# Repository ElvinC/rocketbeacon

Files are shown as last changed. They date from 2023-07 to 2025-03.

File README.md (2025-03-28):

# rocketbeacon
Configurable sub-GHz radio beacon for amateur rocketry.

**Warning: make sure to comply with your local RF regulations. Some frequency bands require an amateur radio license, others have power or duty cycle limitations.**

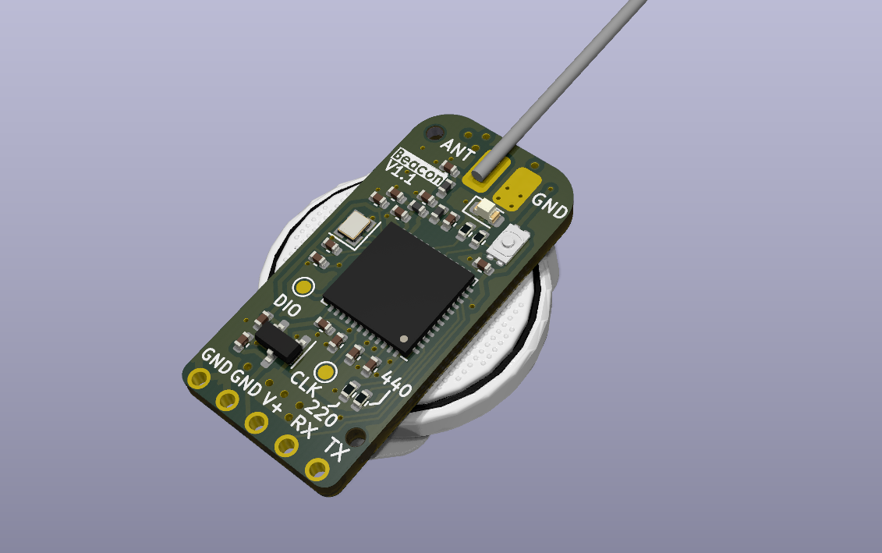
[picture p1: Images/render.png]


## Hardware V1.0
The hardware is designed in KiCad for assembly with JLCPCB. Two versions of the RF front end are available, one optimized for the 220 MHz band and one for the 440 MHz band.

The hardware features:

* STM32WLE5 wireless microcontroller
* Max 22 dBm output power
* CR2032 battery holder
* Can be powered externally by 3.3-5V

## Battery selection and life
**Warning: the beacon doesn't have reverse polarity protection, always double check the battery polarity!** If powered by an external battery (e.g. 1s lipo), connect to the V+ and GND pins. 

CR2032 batteries can't supply much current. When using CR2032 batteries, transmit powers above 16 dBm are not recommended without proper testing. When the voltage drops below 1.8V, the module restarts. An initial delay of a few seconds is thus recommended to allow CR2032 batteries to "recover" after a reset.

To give an idea of the battery life: 3x200 ms beeps at -9, 2, 14 dBm at 4 second intervals achieved 20 hours of battery life with the CR2032. 

Using LiPo batteries, transmit powers up to 22 dBm can be used without issues.

## Assembly V1.1
V1.1 is has some minor tweaks: Larger battery solder pads for improved durability, removal of an unnecessary rx component, and silkscreen tweaks.
The assembled PCB can be ordered by uploading the files from the 1.1 release to JLCPCB. `BOM-beacon-v1.1-440MHz.csv` or `BOM-beacon-v1.1-440MHz.csv` are the BOMs for each frequency version (pick one). Make sure visually that all components (except the 220/440 indicator resistor) are populated.

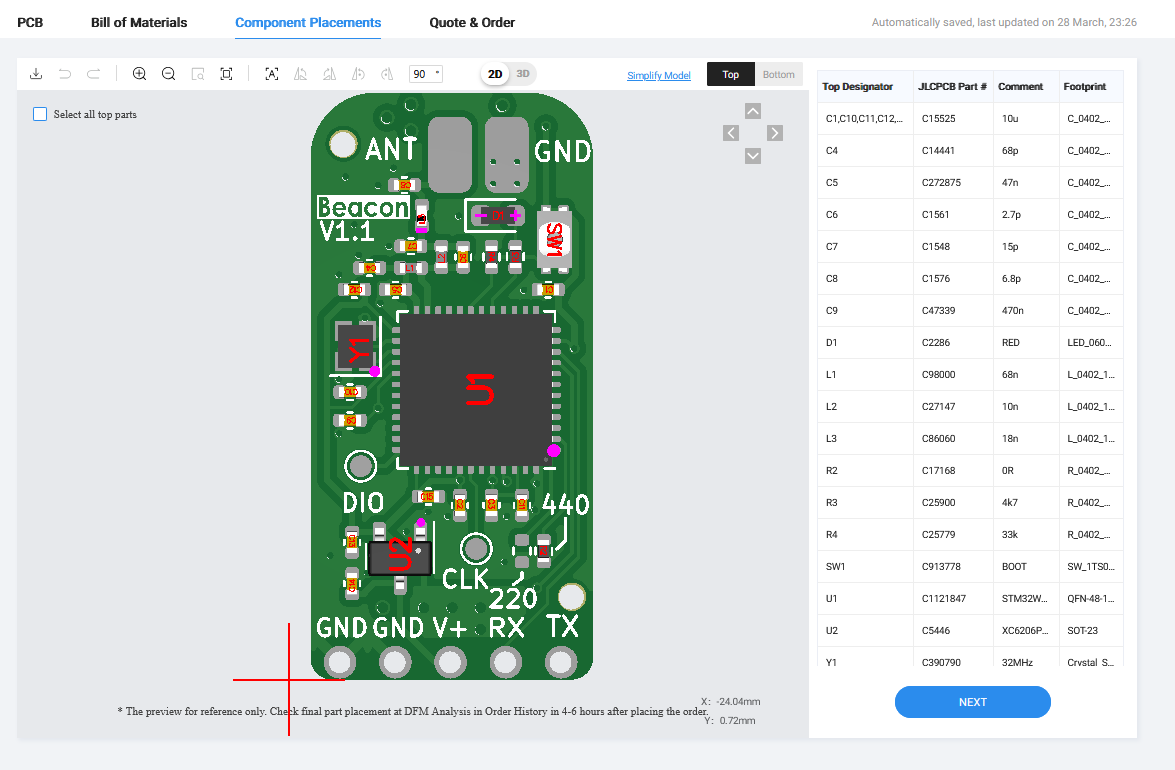
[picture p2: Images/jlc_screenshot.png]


Some BOM parts may be unavailable at the time of ordering, requiring alternative parts to be selected:

* STM32WLE5CBU6 alternatives: STM32WLE5CCU6 (other in the same family should work too without firmware changes)
* Crystal alternatives: Most 32MHz 10pF 10ppm crystals in the 2016 package should work. E.g. S2132000101080 (though default calibration might be off)
* Capacitor alternatives: Same values in the same package
* Inductors: Same values in the same package

Use the following settings when ordering:

* Layers=2
* Thickness=1.6
* Vias=Tented
* Remove order number=Specify a location
* PCBA type=Economic
* Assembly side=Top side
* Tooling holes = Added by Customer

## Assembly V1.0
The assembled PCB can be ordered by uploading the files from `Hardware\beacon\jlcpcb\production_files\V1.0` to JLCPCB. These files are also available in releases as a zip file. `GERBER-beacon.zip` contains the PCB files. For the pick-and-place centroid file, pick either `CPL-beacon-no-pinheader.csv` (cheaper and more compact) or `CPL-beacon-with-pinheader.csv` (assembled with pinheader). `BOM-beacon-v1.0-440MHz.csv` or `BOM-beacon-v1.0-440MHz.csv` are the BOMs for each frequency version (pick one). Make sure visually that all components (except the 220/440 indicator resistor) are populated. If the default STM32WLE5CBU6 is unavailable, the STM32WLE5CCU6 can be selected instead (works with the same firmware).

Use the following settings when ordering:

* Layers=2
* Thickness=1.6
* Vias=Tented
* Remove order number=Specify a location
* PCBA type=Economic
* Assembly side=Top side
* Tooling holes = Added by Customer

## Soldering

Other than the assembled PCB, an antenna is required. For a basic quarter wave copper antenna, you can use `length = 0.95 * 0.25 * speed of light / frequency`, where 0.95 is the velocity factor of copper. E.g.

* For 433 MHz, use a 165mm
* For 220 MHz band, Use 324mm

If powered by a button cell battery, solder on a [MY-2032-12](https://www.lcsc.com/product-detail/Battery-Connectors_MYOUNG-MY-2032-12_C964833.html) battery connector. Other similar CR2032 holders work as well, but may require trimming the solder leads to fit the footprint. Melt a little solder on the negative battery terminal before soldering on the battery holder to ensure proper electrical contact.

## Compile and program
The firmware can be modified and compiled with [STM32CubeIDE](https://www.st.com/en/development-tools/stm32cubeide.html).

The main code is located in `Firmware\Core\Src\main.c`. There are three main functions used to generate RF signals:

* `FSKBeep(int8_t powerdBm, uint32_t toneHz, uint32_t lengthMs)`: Synthesize a FSK sequence of alternating 1s and 0s. With a FM receiver, it sounds like a constant audio tone at `toneHz`.
* `CWBeep(int8_t powerdBm, uint32_t lengthMs)`: Generate a continuous wave tone. E.g. for morse code

Note that the `powerdBm` value can range from -9 to 22 dBm. `HAL_Delay(uint32_t millis)` can be used as delay.

Additionally, `play_morse_word(uint8_t* letters, uint8_t len, bool use_cw)` can be used to send an array of letters as morse (either FM or CW).

The default firmware allows for generation of regular FSK or CW tones at various power levels, with options for transmitting callsigns.

Programming the firmware can be done with [STM32CubeProg](https://www.st.com/en/development-tools/stm32cubeprog.html) and a cheap UART to USB dongle (If you don't have one, search "FTDI adaptor" and get one of the red dongles with 6 pins)

* Disconnect power
* Hold down the button
* Set UART adaptor to output 5V power with the jumper, though 3.3V should work as well.
* Connect the UART adaptor to the beacon (make sure Rx->Tx, Tx->Rx, GND->GND and VCC->V+). If unsoldered, hold them at an angle to ensure proper contact as shown below.
* LED should be continuously ON, indicating it has entered bootloader mode.
* In STM32CubeProg, select the UART option and port. Then connect to the MCU.
* In the Erasing & Programming tab, pick the right firmware `Firmware\Debug\rocketbeacon.elf`, and program
* Cycle power to execute the code.

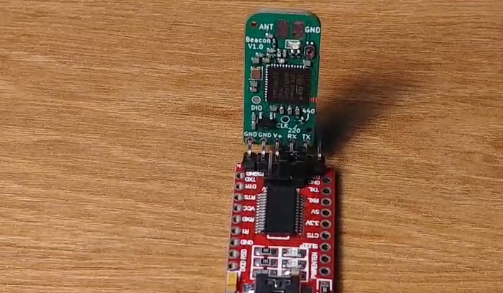
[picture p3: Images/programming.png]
programming


## Reception and tuning
Tune your radio to the programmed frequency. Without calibration, the frequency has a tolerance of roughly +/- 5 KHz in the 70 cm band.

## License and usage
Feel free to use or adapt the hardware design, though if you're a vendor interested in distributing these, please reach out to me at elvin (at) gyroflow.xyz :)

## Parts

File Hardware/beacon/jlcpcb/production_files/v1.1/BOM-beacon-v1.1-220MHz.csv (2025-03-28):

Comment | Designator | Footprint | LCSC
STM32WLE5CBUx | U1 | QFN-48-1EP_7x7mm_P0.5mm_EP5.6x5.6mm | C1121847
68p | C4 | C_0402_1005Metric | C14441
39p | C7 | C_0402_1005Metric | C106223
10u | C1,C10,C11,C12,C13,C14,C15,C2,C3 | C_0402_1005Metric | C15525
8.2p | C6 | C_0402_1005Metric | C325456
12p | C8 | C_0402_1005Metric | C1547
RED | D1 | LED_0603_1608Metric | C2286
33k | R4 | R_0402_1005Metric | C25779
4k7 | R3 | R_0402_1005Metric | C25900
15n | L2 | L_0402_1005Metric | C27143
47n | C5 | C_0402_1005Metric | C272875
32MHz | Y1 | Crystal_SMD_2016-4Pin_2.0x1.6mm | C383840
470n | C9 | C_0402_1005Metric | C47339
XC6206P332MR | U2 | SOT-23 | C5446
36n | L3 | L_0402_1005Metric | C2046147
BOOT | SW1 | SW_1TS026A | C913778
160n | L1 | L_0402_1005Metric | C413908
0R | R1 | R_0402_1005Metric | C17168
DNP | R2 | R_0402_1005Metric
Battery_Cell | BT1 | MY-2032-12

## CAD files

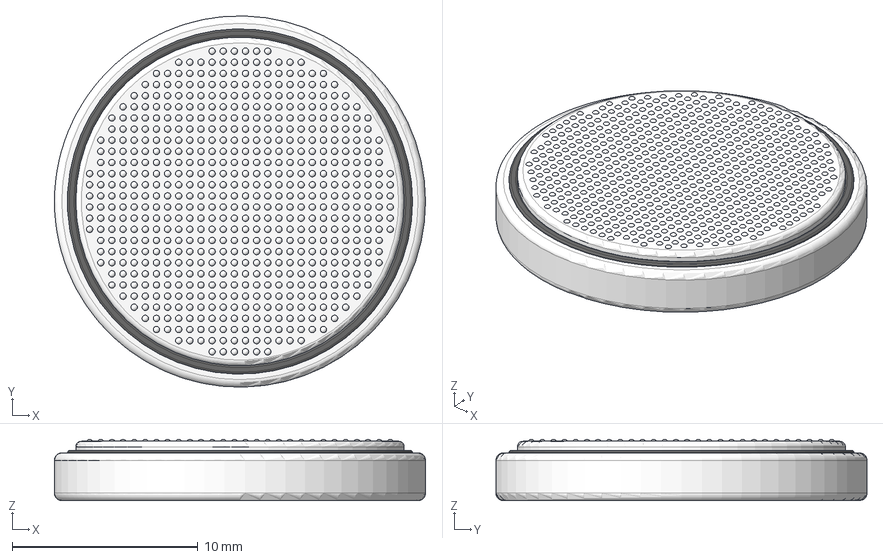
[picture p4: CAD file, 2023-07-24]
Hardware/beacon/3dmodels/cr2032_cell.step
20.0 x 20.0 x 3.30 mm

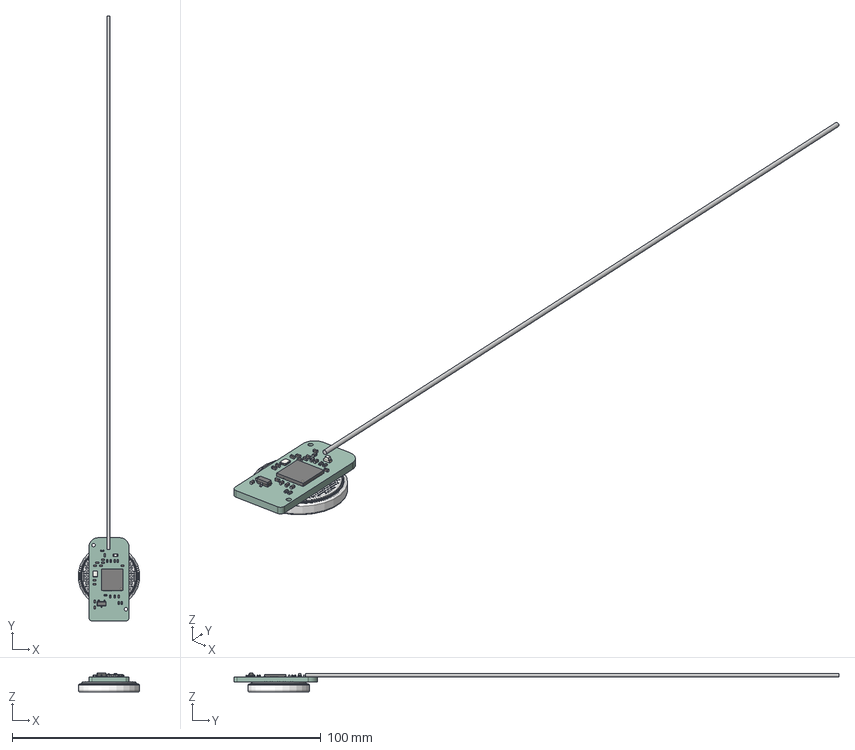
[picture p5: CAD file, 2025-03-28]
Hardware/beacon/beacon_v1.1.step
19.9 x 196.1 x 6.10 mm
L_0402_1005Metric x 3
C_0402_1005Metric x 15
QFN-48-1EP_7x7mm_Pitch0.5mm
R_0402_1005Metric x 4
SOT_23
Crystal_SMD_3225-4Pin_3.2x2.5mm
LED_0603_1608Metric
whipantenna v1
_autosave-beacon_PCB

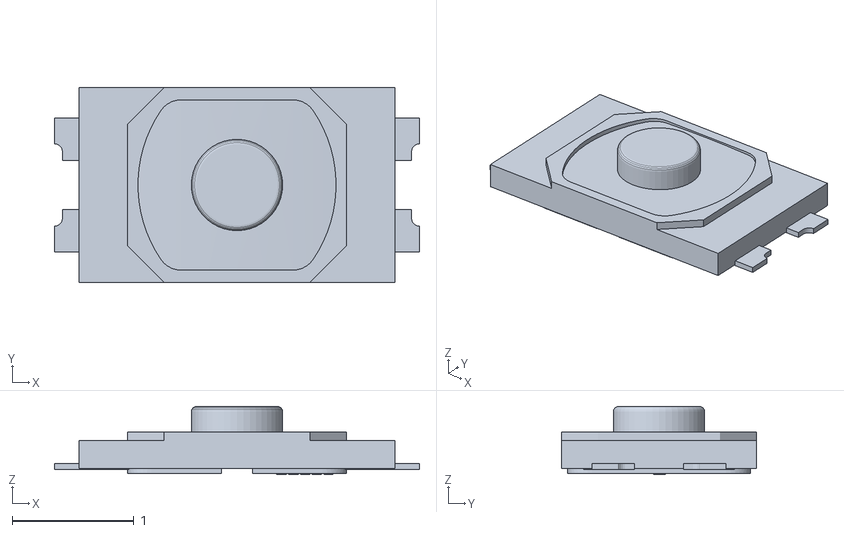
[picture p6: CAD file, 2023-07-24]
Hardware/beacon/3dmodels/1TS026A-1000-0550-CT.obj
3.00 x 1.60 x 0.56

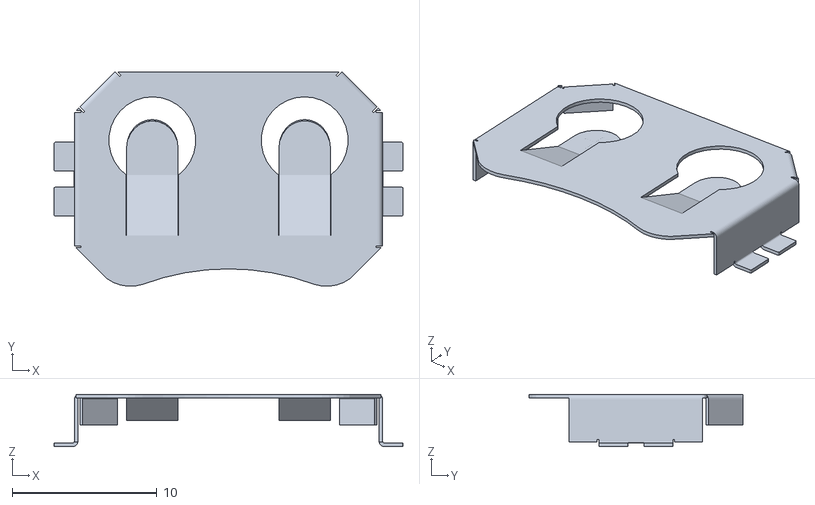
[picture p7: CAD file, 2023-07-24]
Hardware/beacon/3dmodels/cr2032.obj
24.1 x 14.8 x 3.60

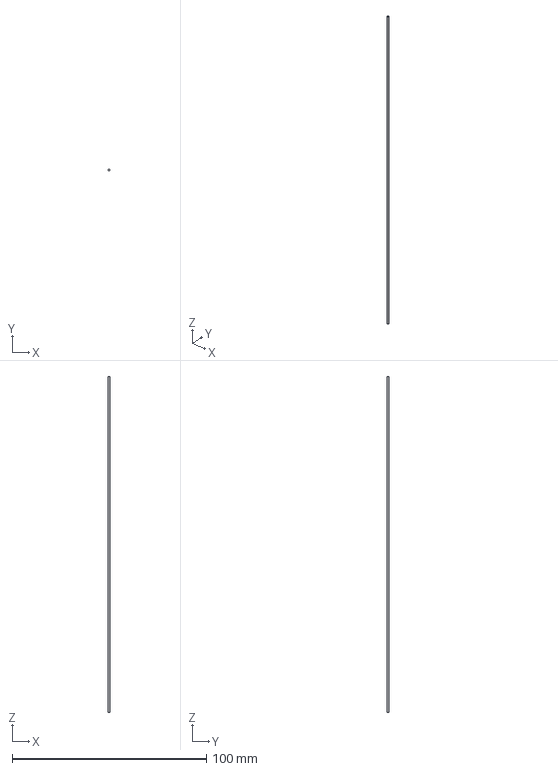
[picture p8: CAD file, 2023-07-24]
Hardware/beacon/3dmodels/whipantenna.step
0.999 x 1 x 173.0 mm

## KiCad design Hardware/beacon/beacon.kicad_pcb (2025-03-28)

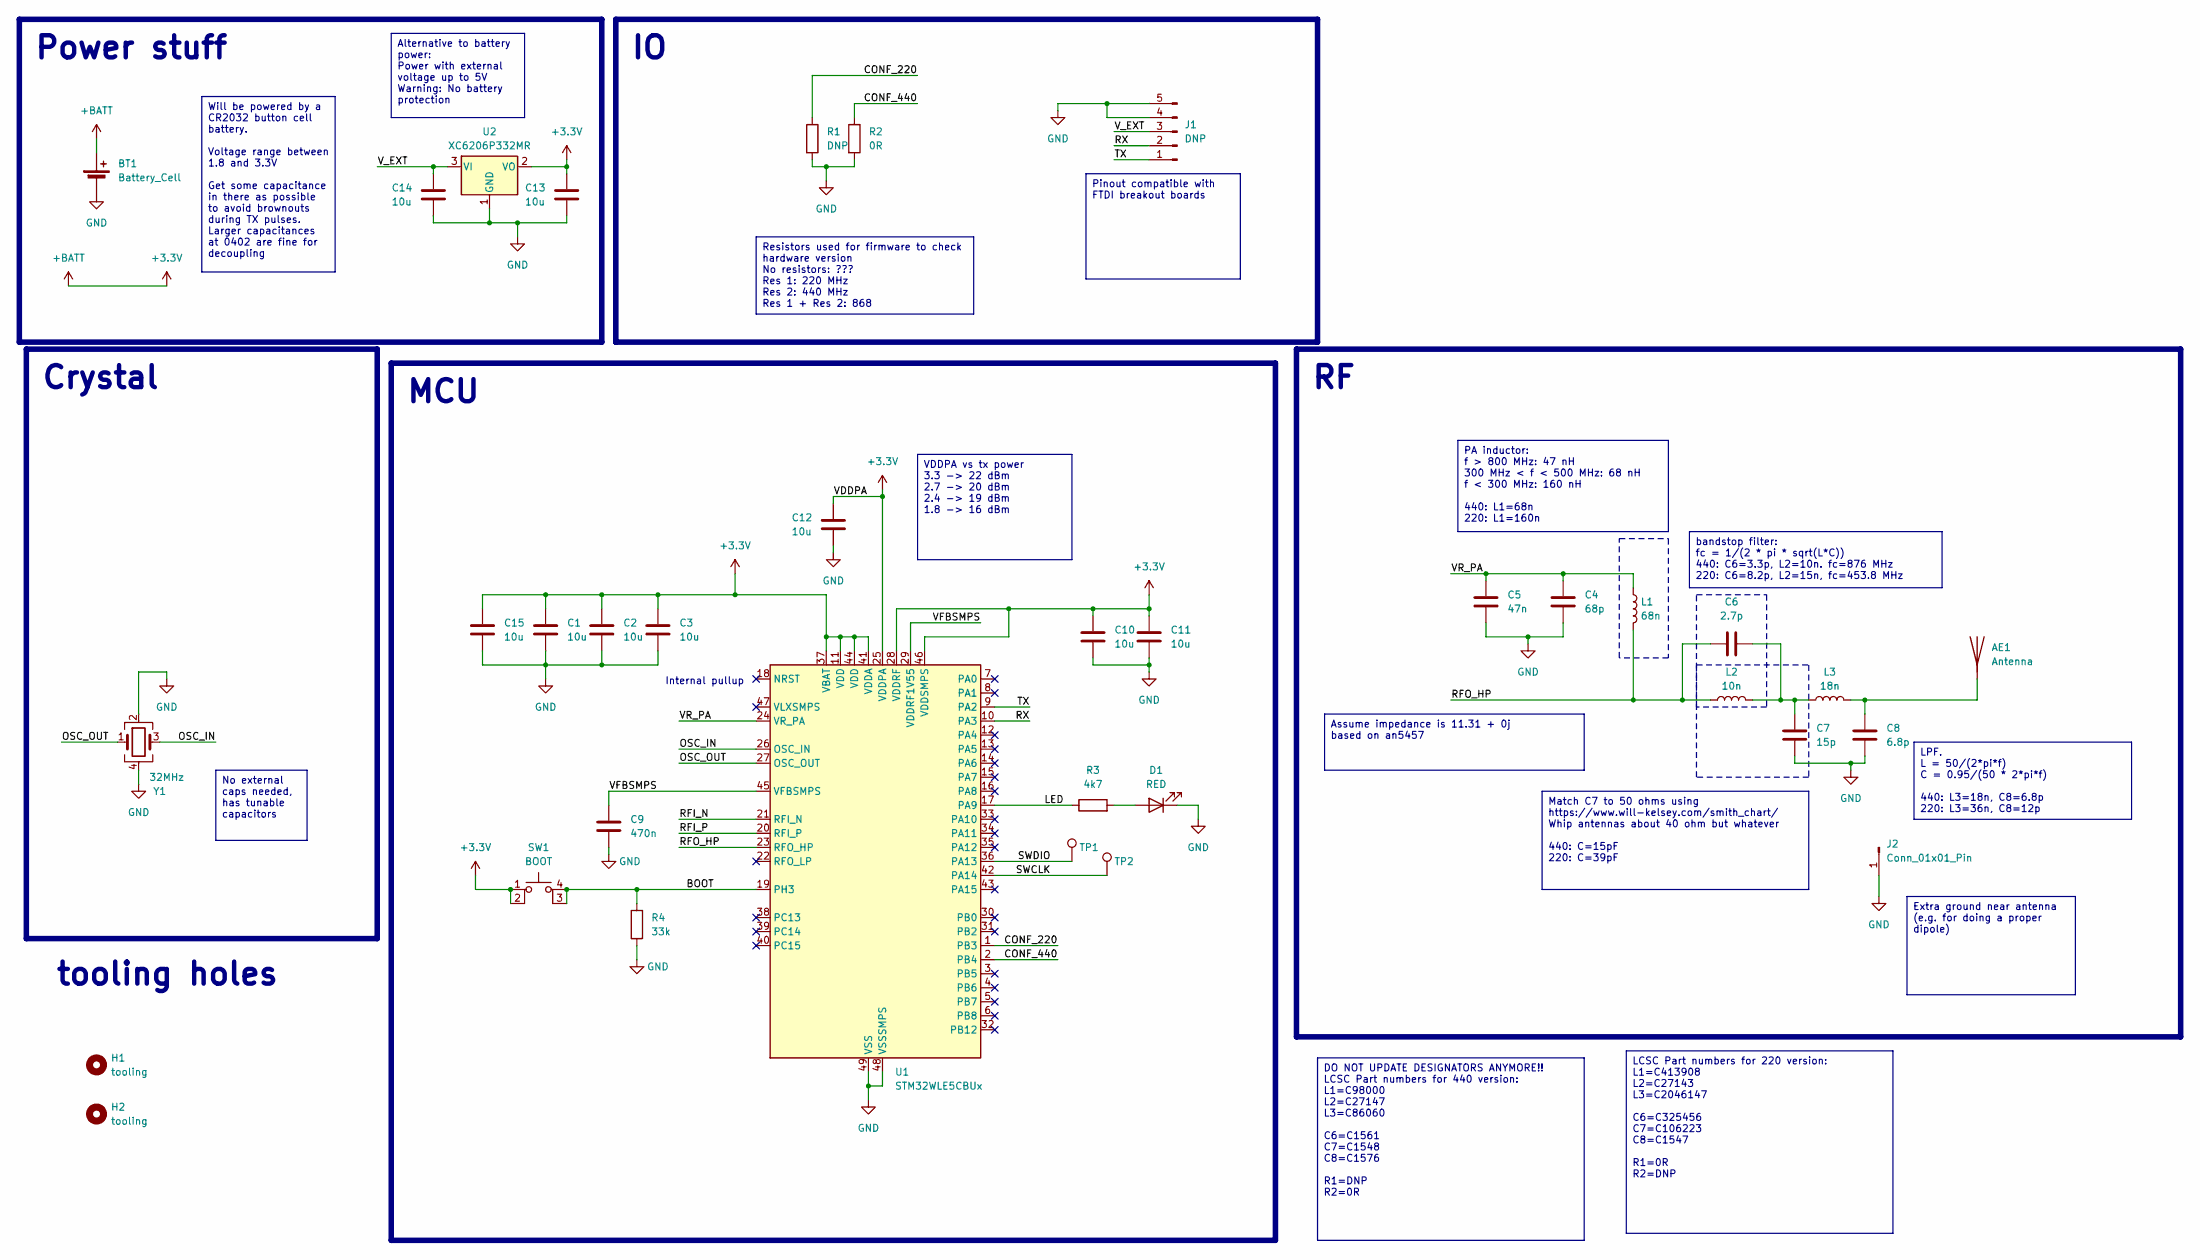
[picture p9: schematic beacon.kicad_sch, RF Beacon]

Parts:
AE1: Antenna; whip_antenna
BT1: Battery_Cell; MY-2032-12
C1, C2, C3, C10, C11, C12, C13, C14, C15: 10u; C_0402_1005Metric
C4: 68p; C_0402_1005Metric
C5: 47n; C_0402_1005Metric
C6: 2.7p; C_0402_1005Metric
C7: 15p; C_0402_1005Metric
C8: 6.8p; C_0402_1005Metric
C9: 470n; C_0402_1005Metric
D1: RED; LED_0603_1608Metric
H1, H2: tooling; toolinghole
J1: DNP; PinHeader_1x05_P2.54mm_Horizontal
J2: Conn_01x01_Pin; small_pad
L1: 68n; L_0402_1005Metric
L2: 10n; L_0402_1005Metric
L3: 18n; L_0402_1005Metric
R1: DNP; R_0402_1005Metric
R2: 0R; R_0402_1005Metric
R3: 4k7; R_0402_1005Metric
R4: 33k; R_0402_1005Metric
SW1: BOOT; SW_1TS026A
TP1, TP2: TestPoint_Pad_D1.0mm
U1: STM32WLE5CBUx; QFN-48-1EP_7x7mm_P0.5mm_EP5.6x5.6mm
U2: XC6206P332MR; SOT-23
Y1: 32MHz; Crystal_SMD_2016-4Pin_2.0x1.6mm; LCSC C383840

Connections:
+3.3V: BT1.1 (+), C1.1, C2.1, C3.1, C10.1, C11.1, C12.1, C13.1, C15.1, SW1.1, SW1.2, U1.11 (VDD), U1.25 (VDDPA), U1.28 (VDDRF), U1.37 (VBAT), U1.41 (VDDA), U1.44 (VDD), U1.46 (VDDSMPS), U2.2 (VO)
/BOOT: R4.2, SW1.3 (K), SW1.4 (A), U1.19 (PH3)
/CONF_220: R1.1, U1.1 (PB3)
/CONF_440: R2.1, U1.2 (PB4)
/LED: R3.1, U1.17 (PA9)
/OSC_IN: U1.26 (OSC_IN), Y1.3
/OSC_OUT: U1.27 (OSC_OUT), Y1.1
/RFI_N: U1.21 (RFI_N)
/RFI_P: U1.20 (RFI_P)
/RFO_HP: C6.1, L1.2, L2.1, U1.23 (RFO_HP)
/RX: J1.2, U1.10 (PA3)
/SWCLK: TP2.1, U1.42 (PA14)
/SWDIO: TP1.1, U1.36 (PA13)
/TX: J1.1, U1.9 (PA2)
/VFBSMPS: C9.1, U1.29 (VDDRF1V55), U1.45 (VFBSMPS)
/VR_PA: C4.1, C5.1, L1.1, U1.24 (VR_PA)
/V_EXT: C14.1, J1.3, U2.3 (VI)
GND: BT1.2 (-), C1.2, C2.2, C3.2, C4.2, C5.2, C7.2, C8.2, C9.2, C10.2, C11.2, C12.2, C13.2, C14.2, C15.2, D1.1 (K), J1.4, J1.5, J2.1, R1.2, R2.2, R4.1, U1.48 (VSSSMPS), U1.49 (VSS), U2.1 (GND), Y1.2, Y1.4
unnamed: AE1.1 (A), C8.1, L3.2
unnamed: C6.2, C7.1, L2.2, L3.1
unnamed: D1.2 (A), R3.2

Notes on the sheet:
No external caps needed, has tunable capacitors
Match C7 to 50 ohms using https://www.will-kelsey.com/smith_chart/ Whip antennas about 40 ohm but whatever 440: C=15pF 220: C=39pF
Resistors used for firmware to check hardware version No resistors: ??? Res 1: 220 MHz Res 2: 440 MHz Res 1 + Res 2: 868
PA inductor: f > 800 MHz: 47 nH 300 MHz < f < 500 MHz: 68 nH f < 300 MHz: 160 nH 440: L1=68n 220: L1=160n
Extra ground near antenna (e.g. for doing a proper dipole)
bandstop filter: fc = 1/(2 * pi * sqrt(L*C)) 440: C6=3.3p, L2=10n. fc=876 MHz 220: C6=8.2p, L2=15n, fc=453.8 MHz
VDDPA vs tx power 3.3 -> 22 dBm 2.7 -> 20 dBm 2.4 -> 19 dBm 1.8 -> 16 dBm
LCSC Part numbers for 220 version: L1=C413908 L2=C27143 L3=C2046147 C6=C325456 C7=C106223 C8=C1547 R1=0R R2=DNP
Will be powered by a CR2032 button cell battery. Voltage range between 1.8 and 3.3V Get some capacitance in there as possible to avoid brownouts during TX pulses. Larger capacitances at 0402 are fine for decoupling
Assume impedance is 11.31 + 0j based on an5457
LPF. L = 50/(2*pi*f) C = 0.95/(50 * 2*pi*f) 440: L3=18n, C8=6.8p 220: L3=36n, C8=12p
Pinout compatible with FTDI breakout boards
Alternative to battery power: Power with external voltage up to 5V Warning: No battery protection
DO NOT UPDATE DESIGNATORS ANYMORE!! LCSC Part numbers for 440 version: L1=C98000 L2=C27147 L3=C86060 C6=C1561 C7=C1548 C8=C1576 R1=DNP R2=0R
tooling holes
Power stuff
MCU
Crystal
Internal pullup

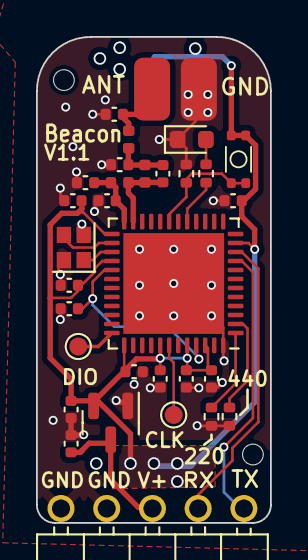
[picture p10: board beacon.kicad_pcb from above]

Board: 2 copper layers, 13.0 x 27.0 mm, 35 parts (1 on the bottom side), 19 nets.

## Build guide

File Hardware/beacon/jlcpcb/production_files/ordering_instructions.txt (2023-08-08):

JLCPCB Ordering options. If not specified, use defaults.

Layers=2
Thickness=1.6
Vias=Tented
Remove order number=Specify a location
PCBA type=Economic
Assembly side=Top side
Tooling holes = Added by Customer

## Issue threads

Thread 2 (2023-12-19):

Issue with ordering from JLCPCB

AD2GF, 2023-12-19:
I attempted to order the 440MHz beacon from JLCPCB, but due to the component 'R2' I am unable to select Economic PCB Assembly, apparently due to the small footprint size of the component. Changing to Standard PCB Assembly ends up adding $50 to the order. The component has a resistance of zero ohms, and it says in the schematic that its only used for telling the firmware whether the beacon is 220MHz/440MHz. Therefore, I plan on removing the resistor from the order, and just bridging the 440MHz pads with solder. I just wanted to confirm whether or not it is safe to do this.

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
ㅤ
ㅤ

ㅤ

In addition, there are 5 components that JLCPCB is unable to find a part for. I assume that the whip antenna, tooling holes, and DNP resistor are not meant to actually populate the PCB, but I wasn't sure if the small connection pad was also supposed to show up as missing.
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

ElvinC, 2023-12-19:
Looks like it selected the wrong package for some reason for the resistor (currently just a visual indicator and not actually implemented in the firmware). You can use C17168 for the 0402 0R resistor. I'll fix the bom files with the proper part numbers at some point

ElvinC, 2023-12-19:
Out of curiosity, how did you find out about this project?

justinkoshy, 2023-12-19:
I was looking for a cheap RDF tracker, there was a thread in the r/rocketry subreddit linking this github. Thanks for the help!

ElvinC, 2023-12-20:
Just keeping this open as a reminder to fix the BOM stuff

Closed 2025-03-28.

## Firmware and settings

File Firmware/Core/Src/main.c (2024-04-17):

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
/* Includes ------------------------------------------------------------------*/
#include "main.h"

/* USER CODE BEGIN Includes */
#include <stdbool.h>
#include <string.h>
#include <math.h>
/* USER CODE END Includes */

ADC_HandleTypeDef hadc;

CRC_HandleTypeDef hcrc;

SUBGHZ_HandleTypeDef hsubghz;

UART_HandleTypeDef huart2;

void SystemClock_Config(void);
static void MX_GPIO_Init(void);
static void MX_ADC_Init(void);
static void MX_SUBGHZ_Init(void);
static void MX_USART2_UART_Init(void);
static void MX_CRC_Init(void);
/* USER CODE BEGIN PFP */

void SetStandbyXOSC();
void SetPacketTypeLora();
void SetPacketTypeFSK();
uint32_t ComputeRfFreq(double frequencyMhz);
void SetRfFreq(uint32_t rfFreq);
void SetPaLowPower();
void SetPa22dB();
void SetTxPower(int8_t powerdBm);
void SetContinuousWave();
void SetTxInfinitePreamble();
void SetTx(uint32_t timeout);
void SetRx(uint32_t timeout);
void SetModulationParamsLora(const uint8_t params[4]);
void SetModulationParamsFSK(uint32_t bitrate, uint8_t pulseshape, uint8_t bandwidth, uint32_t freq_dev);
void SetPacketParamsLora(uint16_t preamble_length, bool header_fixed, uint8_t payload_length, bool crc_enabled, bool invert_iq);
void FSKBeep(int8_t powerdBm, uint32_t toneHz, uint32_t lengthMs);
void CWBeep(int8_t powerdBm, uint32_t lengthMs);

/* USER CODE END PFP */

/* USER CODE BEGIN 0 */

// standard frequencies. Note: zero indexed.
const double LPD433[69] = {
    433.075, 433.100, 433.125, 433.150, 433.175, 433.200, 433.225, 433.250, 433.275, 433.300, // 1-10
    433.325, 433.350, 433.375, 433.400, 433.425, 433.450, 433.475, 433.500, 433.525, 433.550, // 11-20
    433.575, 433.600, 433.625, 433.650, 433.675, 433.700, 433.725, 433.750, 433.775, 433.800, // 21-30
    433.825, 433.850, 433.875, 433.900, 433.925, 433.950, 433.975, 434.000, 434.025, 434.050, // 31-40
    434.075, 434.100, 434.125, 434.150, 434.175, 434.200, 434.225, 434.250, 434.275, 434.300, // 41-50
    434.325, 434.350, 434.375, 434.400, 434.425, 434.450, 434.475, 434.500, 434.525, 434.550, // 51-60
    434.575, 434.600, 434.625, 434.650, 434.675, 434.700, 434.725, 434.750, 434.775           // 61-69
};

const double PMR446[16] = {
    446.00625, 446.01875, 446.03125, 446.04375, 446.05625, // 1-5
    446.06875, 446.08125, 446.09375, 446.10625, 446.11875, // 6-10
    446.13125, 446.14375, 446.15625, 446.16875, 446.18125, // 11-15
    446.19375 // 16
};

const double FRS[22] = {
    462.5625, 462.5875, 462.6125, 462.6375, 462.6625, 462.6875, 462.7125, 467.5625, 467.5875, 467.6125, // 1-10
    467.6375, 467.6625, 467.6875, 467.7125, 462.5500, 462.5750, 462.6000, 462.6250, 462.6500, 462.6750, // 11-20
    462.7000, 462.7250 // 21-22
};


// letter to morse based on ASCII characters.
// right-terminated by a "1". 1 is dah, 0 is dit.
const uint8_t morse_chars[] = {
    0b11111111,       // Special code for SPACE
    0b10000000,       // N/A
    0b10000000,       // N/A
    0b10000000,       // N/A
    0b10000000,       // N/A
    0b10000000,       // N/A
    0b10000000,       // N/A
    0b10000000,       // N/A
    0b10000000,       // N/A
    0b10000000,       // N/A
    0b10000000,       // N/A
    0b10000000,       // N/A
    0b10000000,       // N/A
    0b10000110,       // - Hyphen sign
    0b10000000,       // N/A
    0b10010100,       // "/" Slash
    0b11111100,       // "0"
    0b01111100,       // "1"
    0b00111100,       // "2"
    0b00011100,       // "3"
    0b00001100,       // "4"
    0b00000100,       // "5"
    0b10000100,       // "6"
    0b11000100,       // "7"
    0b11100100,       // "8"
    0b11110100,       // "9"
    0b10000000,       // N/A
    0b10000000,       // N/A
    0b10000000,       // N/A
    0b10001100,       // "=" BT prosign/Equal sign
    0b10000000,       // N/A
    0b00110010,       // "?" Question mark
    0b10000000,       // N/A
    0b01100000,       // "A"
    0b10001000,       // "B"
    0b10101000,       // "C"
    0b10010000,       // "D"
    0b01000000,       // "E"
    0b00101000,       // "F"
    0b11010000,       // "G"
    0b00001000,       // "H"
    0b00100000,       // "I"
    0b01111000,       // "J"
    0b10110000,       // "K"
    0b01001000,       // "L"
    0b11100000,       // "M"
    0b10100000,       // "N"
    0b11110000,       // "O"
    0b01101000,       // "P"
    0b11011000,       // "Q"
    0b01010000,       // "R"
    0b00010000,       // "S"
    0b11000000,       // "T"
    0b00110000,       // "U"
    0b00011000,       // "V"
    0b01110000,       // "W"
    0b10011000,       // "X"
    0b10111000,       // "Y"
    0b11001000,       // "Z"
    0b10000000,       // N/A
    0b10000000,       // N/A
    0b10000000,       // N/A
    0b10000000,       // N/A
    0b10000000,       // N/A
    0b10000000,       // N/A
    0b01100000,       // "a"
    0b10001000,       // "b"
    0b10101000,       // "c"
    0b10010000,       // "d"
    0b01000000,       // "e"
    0b00101000,       // "f"
    0b11010000,       // "g"
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
};

void LED_on() {
    HAL_GPIO_WritePin(LED_GPIO_Port, LED_Pin, GPIO_PIN_SET);
}
void LED_off() {
    HAL_GPIO_WritePin(LED_GPIO_Port, LED_Pin, GPIO_PIN_RESET);
}

// https://en.wikipedia.org/wiki/Morse_code#/media/File:International_Morse_Code.svg
uint32_t morse_unit_ms = 70;
int8_t morse_power = 10;

void play_morse_char(uint8_t ascii_letter, bool use_cw) {
    uint8_t morse_code = 0b11111111;
    if (ascii_letter > 31 && ascii_letter < 123) {
        morse_code = morse_chars[ascii_letter - 32];
    }

    // space
    if (morse_code == 0b11111111) {
        if (use_cw) {
            HAL_Delay(morse_unit_ms);
        } else {
            //FSKBeep(morse_power, 750, morse_unit_ms);
            HAL_Delay(morse_unit_ms);
        }
        return;
    }
    uint8_t terminatelen = 0;
    for (uint8_t idx = 0; idx < 8; idx++) {
        if (morse_code & (1 << idx)) {
            terminatelen = idx;
            break;
        }
    }

    for (uint8_t i = 7; i > terminatelen; i--) {
    	LED_on();
        if (morse_code & (1 << i)) {
            // make dat
            //printf("-");
            if (use_cw) {
                CWBeep(morse_power, morse_unit_ms * 3);
            } else {
                FSKBeep(morse_power, 400, morse_unit_ms * 3);
            }
        } else {
            // make dit
            //printf(".");
            if (use_cw) {
                CWBeep(morse_power, morse_unit_ms);
            } else {
                FSKBeep(morse_power, 400, morse_unit_ms);
            }
        }
        LED_off();

        // Make delay.
        if (use_cw) {
            HAL_Delay(morse_unit_ms);
        } else {
            HAL_Delay(morse_unit_ms);
            //CWBeep(morse_power, morse_unit_ms);
        }
    }
}

void play_morse_word(uint8_t* letters, uint8_t len, bool use_cw) {
    for (uint8_t i = 0; i < len; i++) {
        play_morse_char(letters[i], use_cw);

        // Space between letters
        if (use_cw) {
            HAL_Delay(morse_unit_ms * 3);
        } else {
            //CWBeep(morse_power, morse_unit_ms);
            HAL_Delay(morse_unit_ms * 3);
        }
    }
}


void rx_test(bool is_tx) {
  LED_on();
  HAL_Delay(100);
  LED_off();
  SetStandbyXOSC();
  HAL_Delay(1);
  SetPacketTypeLora();
  HAL_Delay(1);
  SetRfFreq(ComputeRfFreq(433.250));

  //SetPaLowPower(); // For powers up to 14 dBm
  SetPa22dB(); // Allows powers up to 22 dBm
  HAL_Delay(1);
  SetTxPower(-9);
  HAL_Delay(1);
  uint8_t LORA_SF12_BW62_CR45[4] = {0x0C, 0x03, 0x01, 0x00};
  SetModulationParamsLora(LORA_SF12_BW62_CR45);
  HAL_Delay(1);

  SetPacketParamsLora(4, true, 4, true, false); // Send 4 bytes
  HAL_Delay(1);
  uint8_t buffer[4] = {0x00, 0x00, 0x00, 0x00};
  HAL_SUBGHZ_WriteBuffer(&hsubghz, 0, buffer, 4);


  while (1) {
      if (is_tx) {
          buffer[0] = 0x04; // Led ON
          HAL_SUBGHZ_WriteBuffer(&hsubghz, 0, buffer, 4);
          HAL_Delay(1);
          SetTx(0);
          LED_on();
          HAL_Delay(1000);

      } else {
          SetRx(0);
          HAL_Delay(100);
          HAL_SUBGHZ_ReadBuffer(&hsubghz, 0, buffer, 4);
          if (buffer[0] == 0x04) {
              LED_on();

          } else {
              LED_off();
          }
      }
  }

}

/* USER CODE END 0 */

/**
  * @brief  The application entry point.
  * @retval int
  */
int main(void)
{
  /* MCU Configuration--------------------------------------------------------*/

  /* Reset of all peripherals, Initializes the Flash interface and the Systick. */
  HAL_Init();

  /* Configure the system clock */
  SystemClock_Config();

  /* Initialize all configured peripherals */
  MX_GPIO_Init();
  MX_ADC_Init();
  MX_SUBGHZ_Init();
  MX_USART2_UART_Init();
  MX_CRC_Init();
  /* USER CODE BEGIN 2 */

  // ==========================================
  //      START CHANGING SETTINGS HERE
  // ==========================================

  // Frequency setting in MHz
  // Can be a "standard" frequency, e.g. center_freq = LPD433[20-1]; sets it to LPD433 channel 20 (zero indexed) = 433.550 MHz
  double center_freq = 433.225;

  // max power in dBm, valid values between -9 and 22;
  // If using coin cell batteries, values above 16 dBm are not recommended without testing due to current limitations.
  // Alternatively use external LiPo power
  int maxPower = 10;

  double freq_correction = 0.99999539941; // For tuning frequency

  bool CallsignTF = false;
  uint8_t callsign[] = "nocall";

  int CallsignPeriod = 300; // seconds

  // Continuous Wave (CW) settings
  bool CWbeep = false;
  int CWbeepcount = 4;
  bool CWHigh2Low = true; //if true, start with highest power beep, decrease from there
  int CWbeepOffset = 150; //Hertz
  int CWbeepIndLength = 20; //milliseconds
  int CWbeepGapLength = 20; //milliseconds


  // Frequency-shift keying (FSK) settings. Can be heard with FM receivers
  bool FSKbeep = true;
  int FSKbeepcount = 3;
  bool FSKHigh2Low = false; //if true, start with highest power beep, decrease from there. When true, it maximizes the power of the highest power beep, but makes it harder to read a visible signal indicator on later beeps.
  int FSKbeepIndLength = 250; //milliseconds
  int FSKbeepGapLength = 50; //milliseconds
  bool CustomFSKtones = false;
  int CustomFSKfrequencies[] = {320, 400, 480, 640}; // Must match the length exactly!

  int Period = 2000; //milliseconds
  int StartupWait = 5000; // initial start. A few seconds to allow coin cell batteries to recover in case of brownout resets.

  // ==========================================
  //      STOP CHANGING SETTINGS HERE
  // ==========================================


  //EE_Status ee_status = EE_OK;
  LED_on();
  HAL_Delay(StartupWait);
  LED_off();
  SetStandbyXOSC();
  HAL_Delay(1);
  SetPacketTypeLora();
  HAL_Delay(1);

  //SetPaLowPower(); // For powers up to 14 dBm
  SetPa22dB(); // Allows powers up to 22 dBm
  HAL_Delay(1);
  SetTxPower(-9);
  HAL_Delay(1);

  SetPacketTypeFSK();

  SetModulationParamsFSK(2000,    0x09,     0x1E,      2500);


  //  int FSKtones[12] = {400, 350, 300, 250, 200, 150, 1600, 2000, 2400, 3200, 4000, 4800};
  int FSKtones[FSKbeepcount];
  SetRfFreq(ComputeRfFreq(center_freq * freq_correction));

  memset(FSKtones, 0, sizeof(FSKtones));
  for(int i=0; i<FSKbeepcount; i++){
      int base = floor(i/3);
      int mplr = 1<<base;
      FSKtones[i] = 320*(1 + 0.25*(i-3*floor(i/3)))*mplr;
  }
  if (CustomFSKtones){
      memcpy(FSKtones, CustomFSKfrequencies, sizeof(FSKtones));
  }

  /* USER CODE END 2 */

  /* Infinite loop */
  /* USER CODE BEGIN WHILE */

  /*
  while (1) {
      // Emulate comspec beacon at 40 mW
      LED_on();
      CWBeep(16, 50);
      LED_off();
      HAL_Delay(1000);
  }*/

  int loopCounter = floor(CallsignPeriod * 1000 / Period);

  int gap = Period;
  if(FSKbeep) {
	  gap = gap-(FSKbeepIndLength * FSKbeepcount);
	  gap = gap-(FSKbeepGapLength * (FSKbeepcount-1));
  }
  if(CWbeep) {
	  gap = gap-(CWbeepIndLength * CWbeepcount);
	  gap = gap-(CWbeepGapLength * (CWbeepcount - 1));
  }
  if (CWbeep && FSKbeep) {
	  gap = gap /2;
  }

  int FSKTXpwrs[FSKbeepcount];
  memset(FSKTXpwrs, 0, sizeof(FSKTXpwrs));
  if(FSKbeep){
	  int stepsize = 0;
	  if (FSKbeepcount > 1){
		  stepsize = (31 - 22 + maxPower)/(FSKbeepcount - 1);
	  }
	  for(int i=0; i<FSKbeepcount; i++){
		 FSKTXpwrs[i] = maxPower - stepsize * i;
	  }
  }
  int CWTXpwrs[CWbeepcount];
  memset(CWTXpwrs, 0, sizeof(CWTXpwrs));
  if(CWbeep){
	  int stepsize = 0;
	  if (CWbeepcount > 1){
		  stepsize = (31 - 22 + maxPower)/(CWbeepcount - 1);
	  }
	  for(int i=0; i<CWbeepcount; i++){
		 CWTXpwrs[i] = maxPower - stepsize * i;
	  }
  }

  while (1)
  {
	  if(CallsignTF)
	  {
		  play_morse_word(callsign, sizeof(callsign)-1, false);
	  }

      LED_off();

      HAL_Delay(gap);
      for (int i=0; i<loopCounter-1; i++)
      {
    	  SetRfFreq(ComputeRfFreq(center_freq * freq_correction));
    	  // FSK beeps
    	  if(FSKbeep){
    		  if(FSKHigh2Low){
    			  for (int j=0; j<FSKbeepcount; j++){
    				  LED_on();
    				  FSKBeep(FSKTXpwrs[j], FSKtones[j], FSKbeepIndLength);
    				  LED_off();
    				  HAL_Delay(FSKbeepGapLength);
    			  }
    		  }
    		  else {
    			  for (int j=0; j<FSKbeepcount; j++){
    				  LED_on();
    				  FSKBeep(FSKTXpwrs[FSKbeepcount-1-j], FSKtones[j], FSKbeepIndLength);
    				  LED_off();
    				  HAL_Delay(FSKbeepGapLength);
    			  }
    		  }
    		  HAL_Delay(gap);
    	  }
    	  if(CWbeep){
    		  if(CWHigh2Low){
    			  for (int j=0; j<CWbeepcount; j++){
    				  LED_on();
    				  SetRfFreq(ComputeRfFreq((center_freq + 0.000001*CWbeepOffset*j) * freq_correction));
    				  CWBeep(CWTXpwrs[j], CWbeepIndLength);
    				  LED_off();
    				  HAL_Delay(CWbeepGapLength);
    			  }
    		  }
    		  else{
    			  for (int j=0; j<CWbeepcount; j++){
    				  LED_on();
    				  SetRfFreq(ComputeRfFreq((center_freq + 0.000001*CWbeepOffset*j) * freq_correction));
    				  CWBeep(CWTXpwrs[CWbeepcount-1-j], CWbeepIndLength);
    				  LED_off();
    				  HAL_Delay(CWbeepGapLength);
    			  }
    		  }
    		  HAL_Delay(gap);
    	  }
    	  // CW beeps
/*    	  LED_on();
          FSKBeep(-9, 400, 150);
          LED_off();

          HAL_Delay(100);

          LED_on();
          FSKBeep(7, 500, 150);
          LED_off();

          HAL_Delay(100);

          LED_on();
          FSKBeep(22, 600, 200);
          LED_off();

          HAL_Delay(1000);

          LED_on();
          CWBeep(22, 25);
          LED_off();
          HAL_Delay(25);
          SetRfFreq(ComputeRfFreq((center_freq + 0.0002) * freq_correction));
          LED_on();
          CWBeep(11, 25);
          LED_off();
          HAL_Delay(25);
          SetRfFreq(ComputeRfFreq((center_freq + 0.0004) * freq_correction));
          LED_on();
          CWBeep(1, 25);
          LED_off();
          HAL_Delay(25);
          SetRfFreq(ComputeRfFreq((center_freq + 0.0006) * freq_correction));
          LED_on();
          CWBeep(-9, 25);
          LED_off();

          HAL_Delay(2000);
*/
      }

    /* USER CODE END WHILE */

    /* USER CODE BEGIN 3 */
  }
  /* USER CODE END 3 */
}

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
/* USER CODE BEGIN 4 */
void SetStandbyXOSC() {
    uint8_t txbuf[2] = {0x80, 0x01};
    HAL_SUBGHZ_ExecSetCmd(&hsubghz, txbuf[0], txbuf+1, sizeof(txbuf)-1);
}

void SetPacketTypeLora() {
    uint8_t txbuf[2] = {0x8A, 0x01};
    HAL_SUBGHZ_ExecSetCmd(&hsubghz, txbuf[0], txbuf+1, sizeof(txbuf)-1);
}

void SetPacketTypeFSK() {
    uint8_t txbuf[2] = {0x8A, 0x00};
    HAL_SUBGHZ_ExecSetCmd(&hsubghz, txbuf[0], txbuf+1, sizeof(txbuf)-1);
}

uint32_t ComputeRfFreq(double frequencyMhz) {
    return (uint32_t)(frequencyMhz * 1048576L); //2^25/(32e6)
}

void SetRfFreq(uint32_t rfFreq) {
    uint8_t txbuf[5] = {0x86, (rfFreq & 0xFF000000) >> 24, (rfFreq & 0x00FF0000) >> 16, (rfFreq & 0x0000FF00) >> 8, rfFreq & 0x000000FF};
    HAL_SUBGHZ_ExecSetCmd(&hsubghz, txbuf[0], txbuf+1, sizeof(txbuf)-1);
}

void SetPaLowPower() {
    // set Pa to 14 dB.
    uint8_t txbuf[5] = {0x95, 0x02, 0x02, 0x00, 0x01};
    HAL_SUBGHZ_ExecSetCmd(&hsubghz, txbuf[0], txbuf+1, sizeof(txbuf)-1);
}

void SetPa22dB() {
    // set Pa to the highest 22 dBm
    uint8_t txbuf[5] = {0x95, 0x04, 0x07, 0x00, 0x01};
    HAL_SUBGHZ_ExecSetCmd(&hsubghz, txbuf[0], txbuf+1, sizeof(txbuf)-1);
}

void SetTxPower(int8_t powerdBm) {
    // Between -9 and 22
    int8_t power = powerdBm < -9 ? -9 : ((powerdBm > 22) ? 22 : powerdBm);
    uint8_t txbuf[3] = {0x8E, (uint8_t) power, 0x02};
    HAL_SUBGHZ_ExecSetCmd(&hsubghz, txbuf[0], txbuf+1, sizeof(txbuf)-1);
}

void SetContinuousWave() {
    uint8_t txbuf[1] = {0xD1};
    HAL_SUBGHZ_ExecSetCmd(&hsubghz, txbuf[0], txbuf, 0);
}

void SetTxInfinitePreamble() {
    uint8_t txbuf[1] = {0xD2};
    HAL_SUBGHZ_ExecSetCmd(&hsubghz, txbuf[0], txbuf, 0);
}

void SetTx(uint32_t timeout) {
    // Timeout * 15.625 µs
    uint8_t txbuf[4] = {0x83, (timeout & 0x00FF0000) >> 16, (timeout & 0x0000FF00) >> 8, timeout & 0x000000FF};
    HAL_SUBGHZ_ExecSetCmd(&hsubghz, txbuf[0], txbuf+1, sizeof(txbuf)-1);
}

void SetRx(uint32_t timeout) {
    // Timeout * 15.625 µs
    // 0x000000 No timeout. Rx Single mode
    // 0xFFFFFF Rx Continuous mode. The device remains in RX mode until the host sends a command to change the operation mode
    uint8_t txbuf[4] = {0x82, (timeout & 0x00FF0000) >> 16, (timeout & 0x0000FF00) >> 8, timeout & 0x000000FF};
    HAL_SUBGHZ_ExecSetCmd(&hsubghz, txbuf[0], txbuf+1, sizeof(txbuf)-1);
}

void SetModulationParamsLora(const uint8_t params[4]) {
    uint8_t txbuf[5] = {0x8B, params[0], params[1], params[2], params[3]};
    HAL_SUBGHZ_ExecSetCmd(&hsubghz, txbuf[0], txbuf+1, sizeof(txbuf)-1);
}

void SetModulationParamsFSK(uint32_t bitrate, uint8_t pulseshape, uint8_t bandwidth, uint32_t freq_dev) {
    uint32_t BR = 32 * 32e6 / bitrate;
    uint32_t fdev = (uint32_t) (freq_dev * 1.048576L); // 2^25/32e6 = 1.048576
    uint8_t txbuf[9] = {0x8B, (BR & 0x00FF0000) >> 16, (BR & 0x0000FF00) >> 8, BR & 0x000000FF, pulseshape, bandwidth, (fdev & 0x00FF0000) >> 16, (fdev & 0x0000FF00) >> 8, fdev & 0x000000FF};
    HAL_SUBGHZ_ExecSetCmd(&hsubghz, txbuf[0], txbuf+1, sizeof(txbuf)-1);
}

void SetPacketParamsLora(uint16_t preamble_length, bool header_fixed, uint8_t payload_length, bool crc_enabled, bool invert_iq) {
    uint8_t txbuf[7] = {0x8C, (uint8_t)((preamble_length >> 8) & 0xFF), (uint8_t)(preamble_length & 0xFF),
                        (uint8_t) header_fixed, payload_length, (uint8_t) crc_enabled, (uint8_t) invert_iq};

    HAL_SUBGHZ_ExecSetCmd(&hsubghz, txbuf[0], txbuf+1, sizeof(txbuf)-1);
}
/*
void WriteBuffer(uint8_t offset, uint8_t *data, uint8_t len) {
    HAL_SUBGHZ_WriteBuffer(&hsubghz, offset, data, len);
}

void ReadBuffer(uint8_t offset, uint8_t *data, uint8_t len) {
    HAL_SUBGHZ_ReadBuffer(&hsubghz, offset, data, len);
}
*/
void FSKBeep(int8_t powerdBm, uint32_t toneHz, uint32_t lengthMs) {
    // assume in standbyXOSC already.
    HAL_Delay(1);
    SetTxPower(powerdBm);
    SetModulationParamsFSK(toneHz*2,    0x09,     0x1E,      2500);
    HAL_Delay(5);
    SetTxInfinitePreamble();
    HAL_Delay(lengthMs);
    SetStandbyXOSC();
    HAL_Delay(5);
}

void CWBeep(int8_t powerdBm, uint32_t lengthMs) {
    HAL_Delay(1);
    SetTxPower(powerdBm);
    HAL_Delay(5);
    SetContinuousWave();
    HAL_Delay(lengthMs);
    SetStandbyXOSC();
    HAL_Delay(5);
}
/* USER CODE END 4 */
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


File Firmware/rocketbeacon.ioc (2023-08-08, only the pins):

Mcu.UserName=STM32WLE5CBUx
PA13.Signal=DEBUG_JTMS-SWDIO
PA14.Signal=DEBUG_JTCK-SWCLK
PA2.Signal=USART2_TX
PA3.Signal=USART2_RX
PA9.GPIO_Label=LED
PA9.Signal=GPIO_Output
PB3.GPIO_Label=CONF_440
PB3.Signal=GPIO_Input
PB4.GPIO_Label=CONF_868
PB4.Signal=GPIO_Input
PH3-BOOT0.GPIO_Label=BOOT
PH3-BOOT0.Signal=GPIO_Input

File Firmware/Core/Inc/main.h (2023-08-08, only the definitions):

#define CONF_440_Pin GPIO_PIN_3
#define CONF_440_GPIO_Port GPIOB
#define CONF_868_Pin GPIO_PIN_4
#define CONF_868_GPIO_Port GPIOB
#define LED_Pin GPIO_PIN_9
#define LED_GPIO_Port GPIOA
#define BOOT_Pin GPIO_PIN_3
#define BOOT_GPIO_Port GPIOH

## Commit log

2023-07-24 Initial version
    [1TS026A-1000-0550-CT.obj, beacon.kicad_pcb, beacon.kicad_sch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]
2023-08-08 Files for version 1
    [beacon.kicad_pcb, beacon.kicad_sch, moxon.scad]
2023-08-08 Add assembly files and edit readme
    [beacon-CuBottom.gbr, beacon-CuTop.gbr, beacon-EdgeCuts.gbr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]
2023-08-25 add csv files
    [BOM-beacon-v1.0-220MHz.csv, BOM-beacon-v1.0-440MHz.csv, BOM-beacon.csv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]
2023-09-16 Add max power setting
2023-09-16 Add battery info to readme
2023-09-16 Decrease default tx power for coin cell batteries
2023-10-27 Add centroid file without pinheader
    [CPL-beacon-no-pinheader.csv, CPL-beacon-with-pinheader.csv, CPL-beacon.csv]
2025-03-28 V1.1 beacon files
    [BOM-beacon-v1.0-220MHz.csv, BOM-beacon-v1.0-440MHz.csv, BOM-beacon-v1.1-220MHz.csv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]
2025-03-28 v1.1 step file and tweaked readme
    [beacon_v1.1.step]

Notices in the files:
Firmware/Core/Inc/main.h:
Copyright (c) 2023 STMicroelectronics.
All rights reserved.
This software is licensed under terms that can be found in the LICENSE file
